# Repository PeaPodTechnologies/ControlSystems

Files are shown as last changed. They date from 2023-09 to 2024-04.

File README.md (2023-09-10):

# PeaPod Microcontroller Software

A library written in Arduino C++ for modular plug-and-play low-level control systems through a high-level API. Implemented with PlatformIO and tested on AVR.

# Overview

The goals of this library are threefold:
1. Error-free asynchronous communication with a **dynamic** list of multiplexers and I2C devices;
2. **Abstraction** from those multiplexer groups into hot-swappable `Module`s, and I2C devices into `Sensor`s (environment variable *getters*) and `Actuator`s (environment variable *setters*);
3. **Mapping** together `Sensor`s and `Actuator`s into coherent `ControlSystem`s: feedback systems, each with a "parameter" that can be set as the target value of the environment variable of interest;

## Installation
> This will eventually be migrated to an Arduino library. For now, see #Development##Installation

# Development

## Testing

`pio test -e peapod`

## API

### Object Instance Tree
```
PeaPod (God Object)
|-ControlSystem*'s HashMap (for instruction handling & calculation)
| |-Control Systems [key: environment variable being controlled]
|   |-Sensor* (envvar getter)
|   |-Actuator* (envvar setter)
|   |-parameter (string)
|   |-target    (float)
|
|-Module List (hardware state change tracking -> Interface lifecycle management)
| |-Sensor* Array
| |-Actuator* Array
| |-Interface* Array (support)
| |-array lengths (byte)
```

### Inheritance Tree

```
Interface
|-ADC
|-EEPROM
|-GPIO
|-PWM
|-Any I2C Sensors/Actuators (multiple inheritance)

Module (MUX device)

Sensor
|-All Sensors

Actuator
|-All Actuators
```

### Dependency Summary

> Not including external libraries or `utils/`.

```
Interface
|-MUX (also included in Interface)
|-All other interfaces
|-All I2C Sensors/Actuators
```

## Style Guide

- Sensor and actuator instance-related code should not be const
- Static API code (i.e. ids, factories) should be const (and preferrably PROGMEM)
- Avoid passing around pointers to const pointers. It's already const.

## Hardware Spec

### Connector Pinouts

- I2C: JST SH 1.00mm 4-pin (1: GND, 2: +5V, 3: SDA, 4: SCL)
- Middleware Output Signals: Molex Micro-Lock PLUS 2-pin (1: Signal, 2: GND)
- Endware Recieving Signals: Molex Micro-Lock PLUS 2-pin (1: GND, 2: Signal)
- Power: Molex Micro-Fit 3.0 2-pin (1: GND, 2: VCC)

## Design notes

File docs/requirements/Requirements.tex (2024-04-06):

\documentclass{../../../../docs/tex/report}
\usepackage{setspace} % Setting line spacing
\usepackage{ulem} % Underline
\usepackage{caption} % Captioning figures
\usepackage{subcaption} % Subfigures
\usepackage{geometry} % Page layout
\usepackage{multicol} % Columned pages
\usepackage{array,etoolbox}
\usepackage{fancyhdr}
\usepackage{enumitem}
\usepackage[toc,page]{appendix}

% Page layout (margins, size, line spacing)
\geometry{letterpaper, left=1in, right=1in, bottom=1in, top=1in}
\setstretch{1.5}

% Headers
\pagestyle{fancy}
\lhead{PeaPod for XYZ - Requirements}
\rhead{PeaPod Technologies Inc.}

% Metric counter, referencing commands
\newcounter{metricnumber}
\setcounter{metricnumber}{1}
\newcommand{\metricrow}{M\arabic{metricnumber}}
\newcommand{\mlabel}[1]{\addtocounter{metricnumber}{-1}\refstepcounter{metricnumber}\label{#1}\addtocounter{metricnumber}{1}}
\newcommand{\mref}[1]{\hyperref[#1]{M\ref{#1}}}

\begin{document}

\begin{titlepage}
    \begin{center}
        \vspace*{1.2cm}

        \textbf{\large{PeaPod for XYZ - Requirements}}

        \vspace{0.5cm}

        Outlining the Implementation-Specific Requirements for a PeaPod XYZ\\

        \textit{Extends: \textbf{PeaPod - Requirements}}

        \vfill
        \input{../../../../docs/tex/documentation/Namecard.tex}
        \vspace{1.25cm}

        Revision 0.1\\
        PeaPod Technologies Inc.\\
        March 31st, 2024

    \end{center}
\end{titlepage}

\thispagestyle{plain}

\tableofcontents
\newpage

\section{Introduction}
\label{sec:intro}

\subsection{Purpose}
\label{sec:purpose}

The purpose of this document is to outline both the category requirements (Section \ref{sec:requirements}) for an implementation of the PeaPod framework (See \textit{PeaPod - Requirements}) that XYZ and the scoped requirements (Section \ref{sec:scope}) for the design being proposed by PeaPod Technologies Inc.: \textbf{PeaPod for XYZ}.

\subsection{Design Paradigm}
\label{sec:structure}

\input{../../../../docs/tex/documentation/DesignParadigm.tex}

\clearpage

\subsection{Scope and Justification}
\label{sec:scope}

\begin{enumerate}[label=SC\arabic*., ref=SC\arabic*]
    \item \label{sc:1} Lorem ipsum dolor sit amet, consectetur adipiscing elit:
    \begin{enumerate}[label=SC3\alph*., ref=SC3\alph*]
        \item \label{sc:1a} Sed auctor, nunc nec ultricies ultricies, nunc nunc ultricies nunc, nec ultricies nunc nunc nec.
    \end{enumerate}
\end{enumerate}

\subsection{Definitions}
\label{sec:definitions}

A number of useful definitions have emerged from the above scoping:
\begin{enumerate}
    \item \textbf{ABC} - Lorem ipsum dolor sit amet, consectetur adipiscing elit.
\end{enumerate}

\clearpage

\section{Framing}
\label{sec:framing}

\subsection{Problem Statement}
\label{sec:opportunity}

Lorem ipsum dolor sit amet, consectetur adipiscing elit. Sed auctor, nunc nec ultricies ultricies, nunc nunc ultricies nunc, nec ultricies nunc nunc nec.

\subsection{Solution Requirements}
\label{sec:requirements}

The following are the overall challenge requirements compiled from A, B, and an excerpt from C:
\begin{enumerate}[label=R\arabic*., ref=R\arabic*]
    \item \label{r:1} \textbf{Must} lorem ipsum dolor sit amet, consectetur adipiscing elit:
    \begin{enumerate}[ref=R1\alph*]
        \item \label{r:1a} \textbf{Should} lorem ipsum dolor sit amet, consectetur adipiscing elit;
    \end{enumerate}
\end{enumerate}

% Change line spacing for the more list-heavy sections
\setstretch{1}
\subsection{Stakeholders and Values}
\label{sec:stakeholders}

\begin{enumerate}[label=S\arabic*., ref=S\arabic*]
    \item \label{s:1} A - Values, etc.
    \item \label{s:2} B - DfX, etc.
\end{enumerate}

\clearpage

\subsection{Problem-Solving Goals}
\label{sec:goals}

% High-Level
\begin{multicols}{2}[]
    \begin{enumerate}[label=HL\arabic*., ref=HL\arabic*]
        \item \label{hl:output} Goal ABC \hfill (\ref{s:1}, \ref{r:1}, \ref{r:1a})
    \end{enumerate}
\end{multicols}

\subsection{Solution Objectives}
\label{sec:objectives}

% Low-Level
\begin{multicols}{2}[]
    \begin{enumerate}[label=LL\arabic*., ref=LL\arabic*]
        \item \label{ll:output_variety} Objective ABC \hfill (\ref{hl:output})
    \end{enumerate}
\end{multicols}

\clearpage

\subsection{Metrics}
\label{sec:metrics}

\begin{tabular}{| @{\makebox[2.4em][c]{\metricrow}} | p{8.7cm} | p{5.9cm} |} 
    \hline
    \multicolumn{1}{| @{\makebox[2.4em][c]{\textbf{\#}}} | l |}{\textbf{Metric}} & \textbf{Units}\\ 
    \hline
    Metric ABC \mlabel{m:constraint} \hfill (\ref{ll:output_variety}) & Yes/No \\
    Metric XYZ \mlabel{m:criteria} \hfill (\ref{ll:output_variety}) & 0 - 100\% \\
    \hline
\end{tabular}

\clearpage

\subsection{Constraints}
\label{sec:constraints}

\begin{tabular}{|l|p{14.35cm}|}
    \hline
    \textbf{Metric} & \textbf{Constraint \hfill Justification} \\
    \hline
    \mref{m:constraint} & Yes \hfill (\ref{s:1})\\
    \hline
\end{tabular}

\subsection{Criteria}
\label{sec:criteria}

\begin{tabular}{|l|p{14.35cm}|}
    \hline
    \textbf{Metric} & \textbf{Criteria \hfill Justification} \\
    \hline
    \mref{m:criteria} & Should Maximize \hfill (\ref{r:1a}) \\
    \hline
\end{tabular}

% Refer to Appendix \ref{sec:assessment} for prototype verification Assessment Criteria (categories, weights, etc.).

\newpage

\section{Reference Designs}

% -------- TEMPLATE --------
% Introduction - Project goal, scope, differences from this project
% Graphics - Design drawings/photos, etc.
% Analysis - Rank the design across each of our metrics
    % TODO: Metrics might be too much, maybe just qualitative analysis based on LLOs?

\subsection{Reference Design XYZ}

Lorem ipsum dolor sit amet, consectetur adipiscing elit. Sed auctor, nunc nec ultricies ultricies, nunc nunc ultricies nunc, nec ultricies nunc nunc nec.

% \newpage

% % References
% \bibliographystyle{IEEEtran}
% \bibliography{references}

\end{document}

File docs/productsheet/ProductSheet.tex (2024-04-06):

\documentclass{../../../../docs/tex/report}
\usepackage{setspace} % Setting line spacing
\usepackage{ulem} % Underline
\usepackage{caption} % Captioning figures
\usepackage{subcaption} % Subfigures
\usepackage{geometry} % Page layout
\usepackage{multicol} % Columned pages
\usepackage{array,etoolbox}
\usepackage{fancyhdr}
\usepackage{enumitem}
\usepackage[toc,page]{appendix}
\setlist{noitemsep}

% Page layout (margins, size, line spacing)
\geometry{letterpaper, left=1in, right=1in, bottom=1in, top=1in}
\setstretch{1}

% Headers
\pagestyle{fancy}
\lhead{PeaPod XYZ}
\rhead{PeaPod Technologies Inc.}

\begin{document}

\begin{titlepage}
    \begin{center}
        \vspace*{1.2cm}

        \textbf{\large{PeaPod XYZ - Product Sheet}}

        \vspace{0.5cm}

        Lorem ipsum dolor sit amet, consectetur adipiscing elit.

        \vfill
        \input{../../../docs/tex/documentation/Namecard.tex}
        \vspace{1.25cm}

        Revision 0.1\\
        PeaPod Technologies Inc.\\
        Month XX, 2024

    \end{center}
\end{titlepage}

\thispagestyle{plain}

\tableofcontents
\clearpage

\section{Product Overview}

\subsection{Introduction}

Lorem ipsum dolor sit amet, consectetur adipiscing elit. Sed auctor, nunc nec ultricies ultricies, nunc nunc ultricies nunc, nec ultricies nunc nunc nec. Sed auctor, nunc nec ultricies ultricies, nunc nunc ultricies nunc, nec ultricies nunc nunc nec. Sed auctor, nunc nec ultricies ultricies, nunc nunc ultricies nunc, nec ultricies nunc nunc nec. Sed auctor, nunc nec ultricies ultricies, nunc nunc ultricies nunc, nec ultricies nunc nunc nec.

\clearpage

% References
\bibliographystyle{IEEEtran}
\bibliography{references}
\end{document}

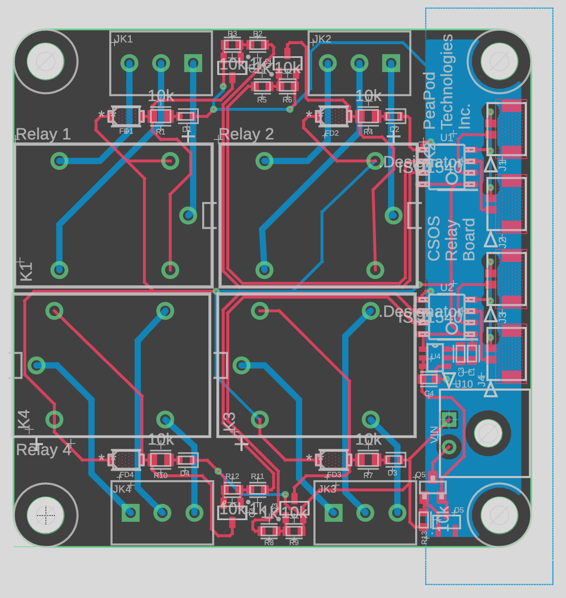
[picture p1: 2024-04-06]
hardware/relay/schematics/relay_brd.png

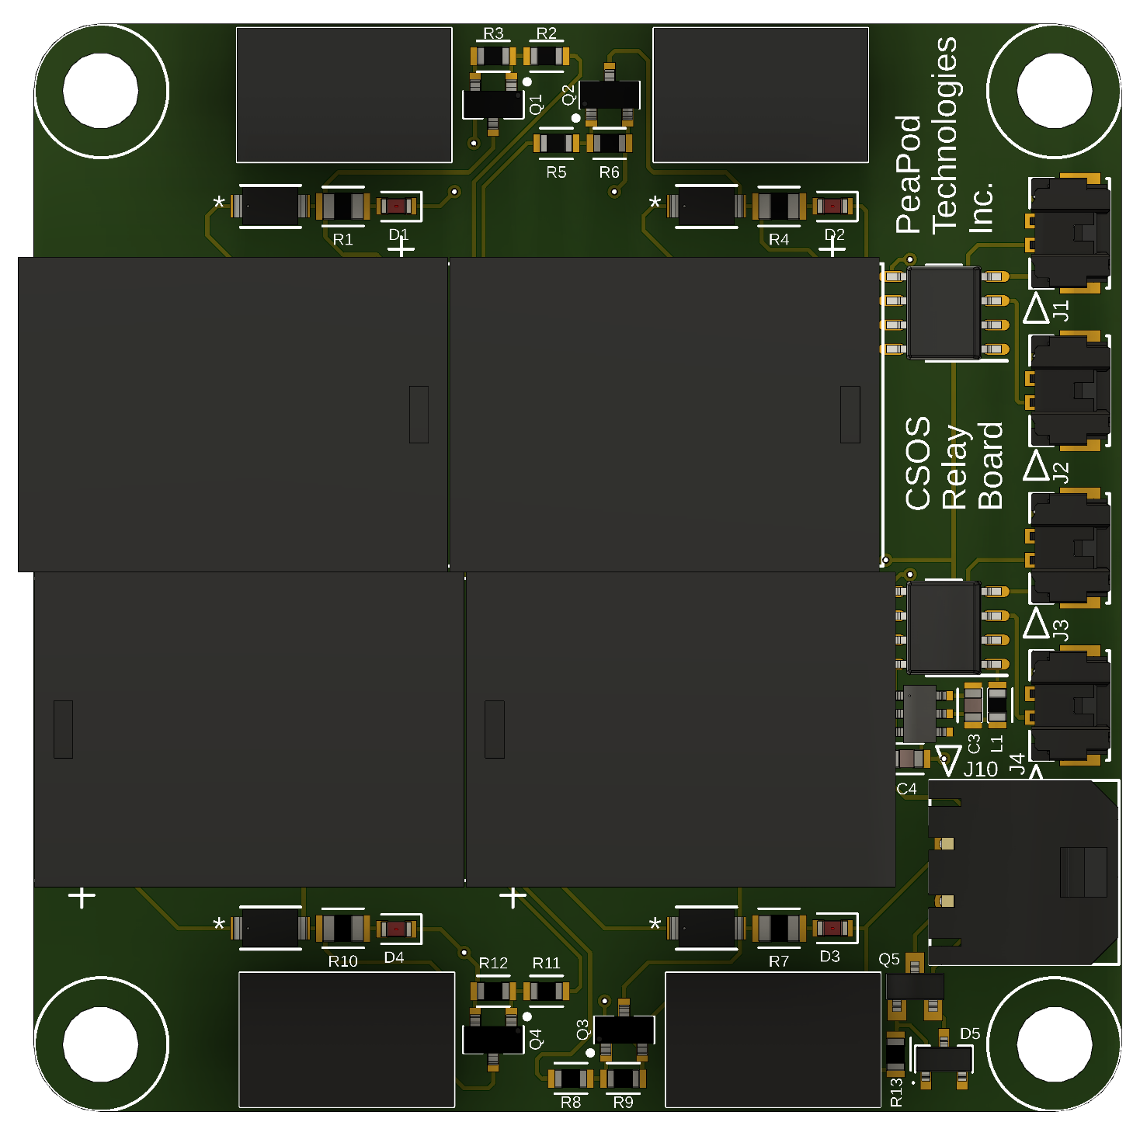
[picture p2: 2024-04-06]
hardware/relay/relay_model.png

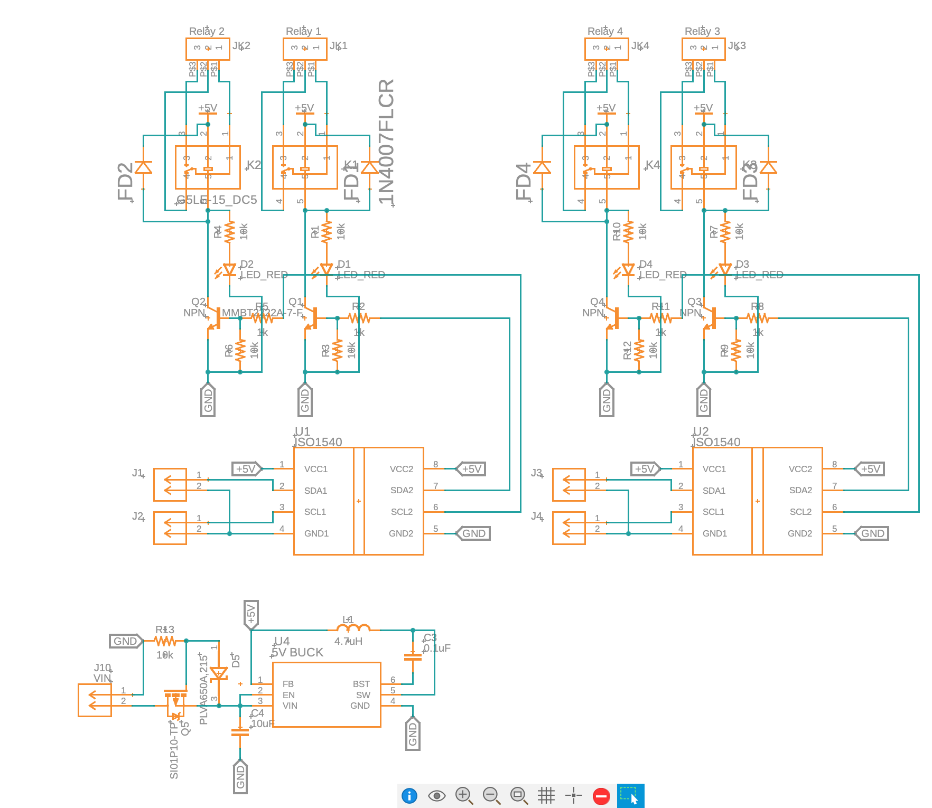
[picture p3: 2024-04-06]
hardware/relay/schematics/relay_sch.png

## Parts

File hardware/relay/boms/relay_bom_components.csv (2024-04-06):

Index | Manufacturer Part Number | Manufacturer Name | Requested Quantity 1 | Pack Quantity 1 | Pack Type 1 | Digi-Key Part Number 1 | Unit Price 1 | Extended Price 1 | Minimum Order Quantity 1 | Reference Designator | Product Notes
1 | PLVA650A,215 | Nexperia USA Inc. | 1 | 1 | Cut Tape (CT) | 1727-5167-1-ND | 0.65000 | $0.65 | 1 | D5
2 | SI01P10-TP | Micro Commercial Co | 1 | 1 | Cut Tape (CT) | 353-SI01P10-TPCT-ND | 0.59000 | $0.59 | 1 | Q5
3 | AP63205WU-7 | Diodes Incorporated | 1 | 1 | Cut Tape (CT) | AP63205WU-7DICT-ND | 1.33000 | $1.33 | 1 | U4
4 | 0436500201 | Molex | 1 | 1 | Tray | WM1865-ND | 2.00000 | $2.00 | 1 | J10
5 | G5LE-14 DC5 | Omron Electronics Inc-EMC Div | 4 | 4 | Tray | Z1011-ND | 2.38000 | $9.52 | 1 | K1,K2,K3,K4
6 | 1N4007FL | SMC Diode Solutions | 4 | 4 | Cut Tape (CT) | 1655-1N4007FLCT-ND | 0.19000 | $0.76 | 1 | FD1,FD2,FD3,FD4
7 | ISO1540D | Texas Instruments | 2 | 2 | Tube | 296-34896-5-ND | 9.46000 | $18.92 | 1 | U1,U2
8 | 5055670271 | Molex | 4 | 4 | Cut Tape (CT) | WM17038CT-ND | 1.32000 | $5.28 | 1 | J1,J2,J3,J4
9 | 0393570003 | Molex | 4 | 4 | Bag | WM7878-ND | 2.67000 | $10.68 | 1 | JK1,JK2,JK3,JK4
10 | CL10B104KB8NNWC | Samsung Electro-Mechanics | 1 | 1 | Cut Tape (CT) | 1276-1935-1-ND | 0.14000 | $0.14 | 1 | C3
11 | LQM18PH4R7MFRL | Murata Electronics | 1 | 1 | Cut Tape (CT) | 490-LQM18PH4R7MFRLCT-ND | 0.57000 | $0.57 | 1 | L1
12 | CL10A106MQ8NNNC | Samsung Electro-Mechanics | 1 | 1 | Cut Tape (CT) | 1276-1119-1-ND | 0.16000 | $0.16 | 1 | C4
13 | MMBT2222A-7-F | Diodes Incorporated | 4 | 4 | Cut Tape (CT) | MMBT2222A-FDICT-ND | 0.21000 | $0.84 | 1 | Q1,Q2,Q3,Q4
14 | LTST-C191KRKT | Lite-On Inc. | 4 | 4 | Cut Tape (CT) | 160-1447-1-ND | 0.40000 | $1.60 | 1 | D1,D2,D3,D4
15 | RC0603FR-0710KL | YAGEO | 5 | 5 | Cut Tape (CT) | 311-10.0KHRCT-ND | 0.15000 | $0.75 | 1 | R3,R6,R9,R12,R13
16 | RC0805FR-0710KL | YAGEO | 4 | 4 | Cut Tape (CT) | 311-10.0KCRCT-ND | 0.15000 | $0.60 | 1 | R1,R4,R7,R10
17 | RC0603FR-071KL | YAGEO | 4 | 4 | Cut Tape (CT) | 311-1.00KHRCT-ND | 0.15000 | $0.60 | 1 | R2,R5,R8,R11

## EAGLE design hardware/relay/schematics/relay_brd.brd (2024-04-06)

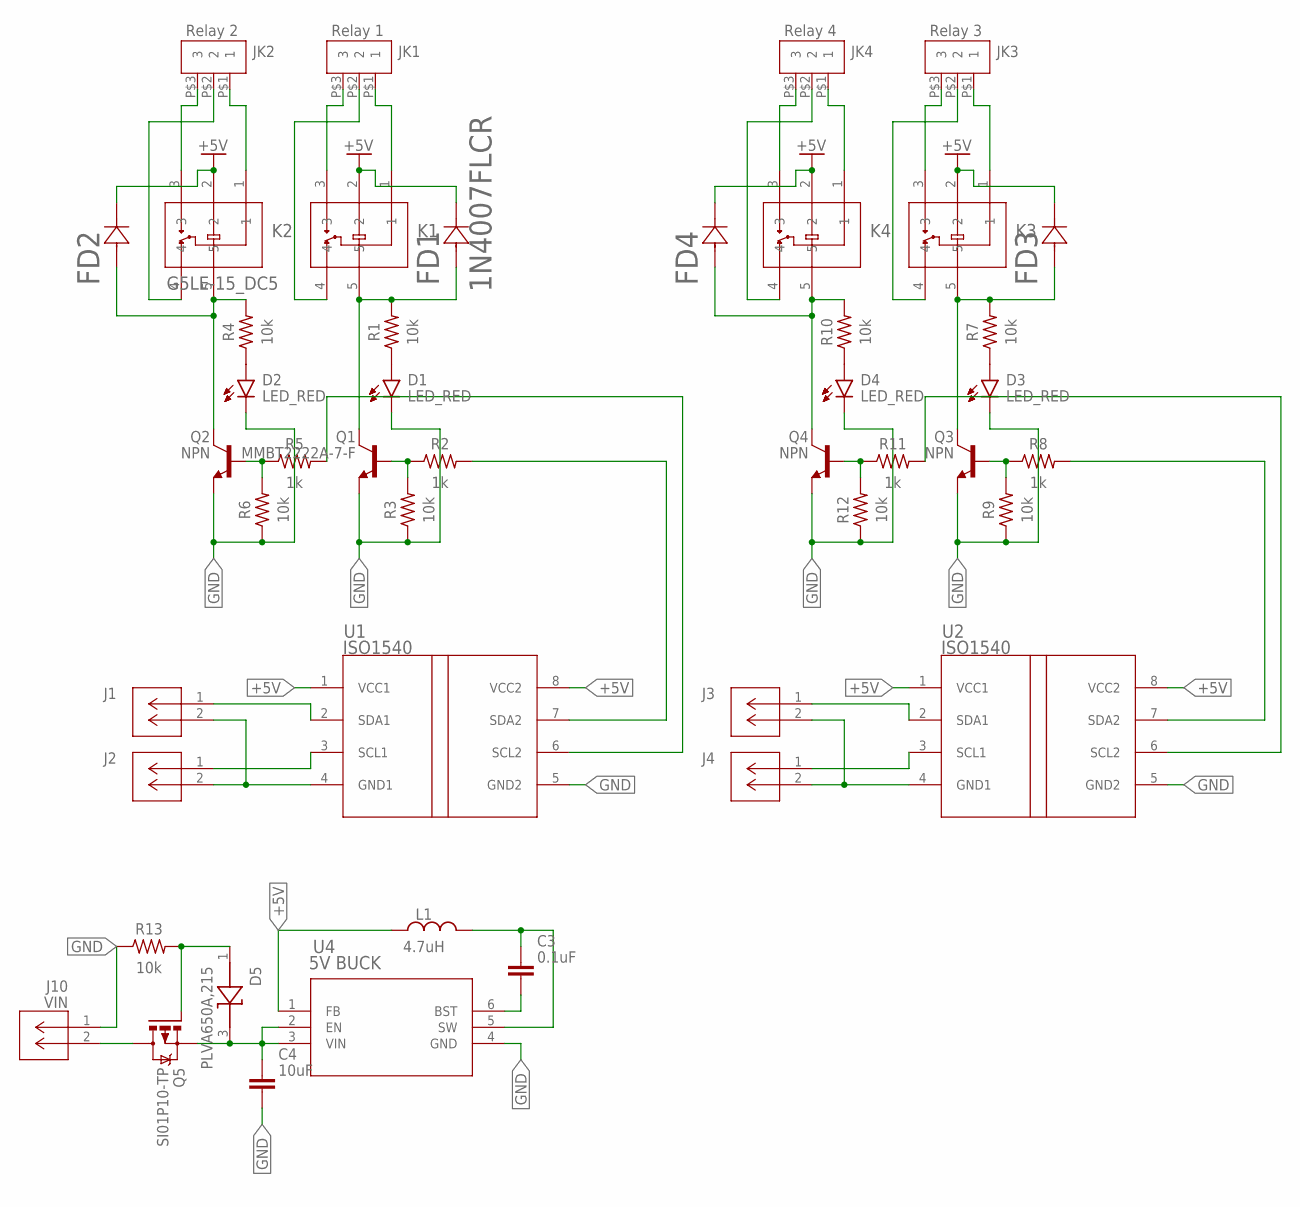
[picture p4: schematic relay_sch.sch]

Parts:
C3: 0.1uF; CAPC1608X85
C4: 10uF; CAPC1608X85
D1, D2, D3, D4: LED_RED; LEDC1608X55N_FLAT-R
D5: PLVA650A,215; SOT95P230X110-3N
FD1: 1N4007FLCR; CR_SOD-123FL_SME-L
FD2, FD3, FD4: 1N4007FLCR_SOD-123FL_SME-L; CR_SOD-123FL_SME-L
J1, J2, J3, J4: MICROLOCK-2PIN; 2PIN
J10: VIN; 2PIN
JK1: Relay 1; TERM-3,5MM
JK2: Relay 2; TERM-3,5MM
JK3: Relay 3; TERM-3,5MM
JK4: Relay 4; TERM-3,5MM
K1, K3, K4: G5LE-14_DC12RELAY_G5LE-1_DC5_OMR; RELAY_G5LE-1_DC5_OMR
K2: G5LE-15_DC5; RELAY_G5LE-1_DC5_OMR
L1: 4.7uH; INDC1608X95N
Q1: MMBT2222A-7-F; SOT95P237X112-3N
Q2, Q3, Q4: NPN; SOT95P237X112-3N
Q5: SI01P10-TP; SOT23
R1, R4, R7, R10: 10k; RESC2012X65
R2, R5, R8, R11: 1k; RESC1608X60
R3, R6, R9, R12, R13: 10k; RESC1608X60
U1, U2: ISO1540; SOIC-8
U4: 5V BUCK; AP63205

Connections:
+5V: FD1.1 (CATHODE), FD2.1 (CATHODE), FD3.1 (CATHODE), FD4.1 (CATHODE), K1.2, K2.2, K3.2, K4.2, L1.1, U1.1 (VCC1), U1.8 (VCC2), U2.1 (VCC1), U2.8 (VCC2), U4.1 (FB)
GND: C4.2, D1.C, D2.C, D3.C, D4.C, J10.1, Q1.2 (E), Q2.2 (E), Q3.2 (E), Q4.2 (E), R3.1, R6.1, R9.1, R12.1, R13.1, U1.5 (GND2), U2.5 (GND2), U4.4 (GND)
unnamed: JK1.P$3 (3), K1.3
unnamed: JK1.P$1 (1), K1.1
unnamed: JK1.P$2 (2), K1.4
unnamed: FD1.2 (ANODE), K1.5, Q1.3 (C), R1.2
unnamed: FD2.2 (ANODE), K2.5, Q2.3 (C), R4.2
unnamed: Q1.1 (B), R2.1, R3.2
unnamed: JK2.P$3 (3), K2.3
unnamed: R2.2, U1.7 (SDA2)
unnamed: J1.1 (2), U1.2 (SDA1)
unnamed: J2.1 (2), U1.3 (SCL1)
unnamed: J1.2 (3), J2.2 (3), U1.4 (GND1)
unnamed: JK2.P$1 (1), K2.1
unnamed: FD4.2 (ANODE), K4.5, Q4.3 (C), R10.2
unnamed: FD3.2 (ANODE), K3.5, Q3.3 (C), R7.2
unnamed: Q2.1 (B), R5.1, R6.2
unnamed: JK2.P$2 (2), K2.4
unnamed: R5.2, U1.6 (SCL2)
unnamed: JK3.P$3 (3), K3.3
unnamed: JK3.P$1 (1), K3.1
unnamed: D2.A, R4.1
unnamed: D3.A, R7.1
unnamed: Q3.1 (B), R8.1, R9.2
unnamed: JK3.P$2 (2), K3.4
unnamed: J3.1 (2), U2.2 (SDA1)
unnamed: R8.2, U2.7 (SDA2)
unnamed: J4.1 (2), U2.3 (SCL1)
unnamed: J3.2 (3), J4.2 (3), U2.4 (GND1)
unnamed: JK4.P$3 (3), K4.3
unnamed: JK4.P$1 (1), K4.1
unnamed: D1.A, R1.1
unnamed: D4.A, R10.1
unnamed: Q4.1 (B), R11.1, R12.2
unnamed: JK4.P$2 (2), K4.4
unnamed: R11.2, U2.6 (SCL2)
unnamed: C3.2, U4.6 (BST)
unnamed: C3.1, L1.2, U4.5 (SW)
unnamed: J10.2, Q5.3 (D)
unnamed: C4.1, D5.3 (C), Q5.2 (S), U4.2 (EN), U4.3 (VIN)
unnamed: D5.1 (A), Q5.1 (G), R13.2

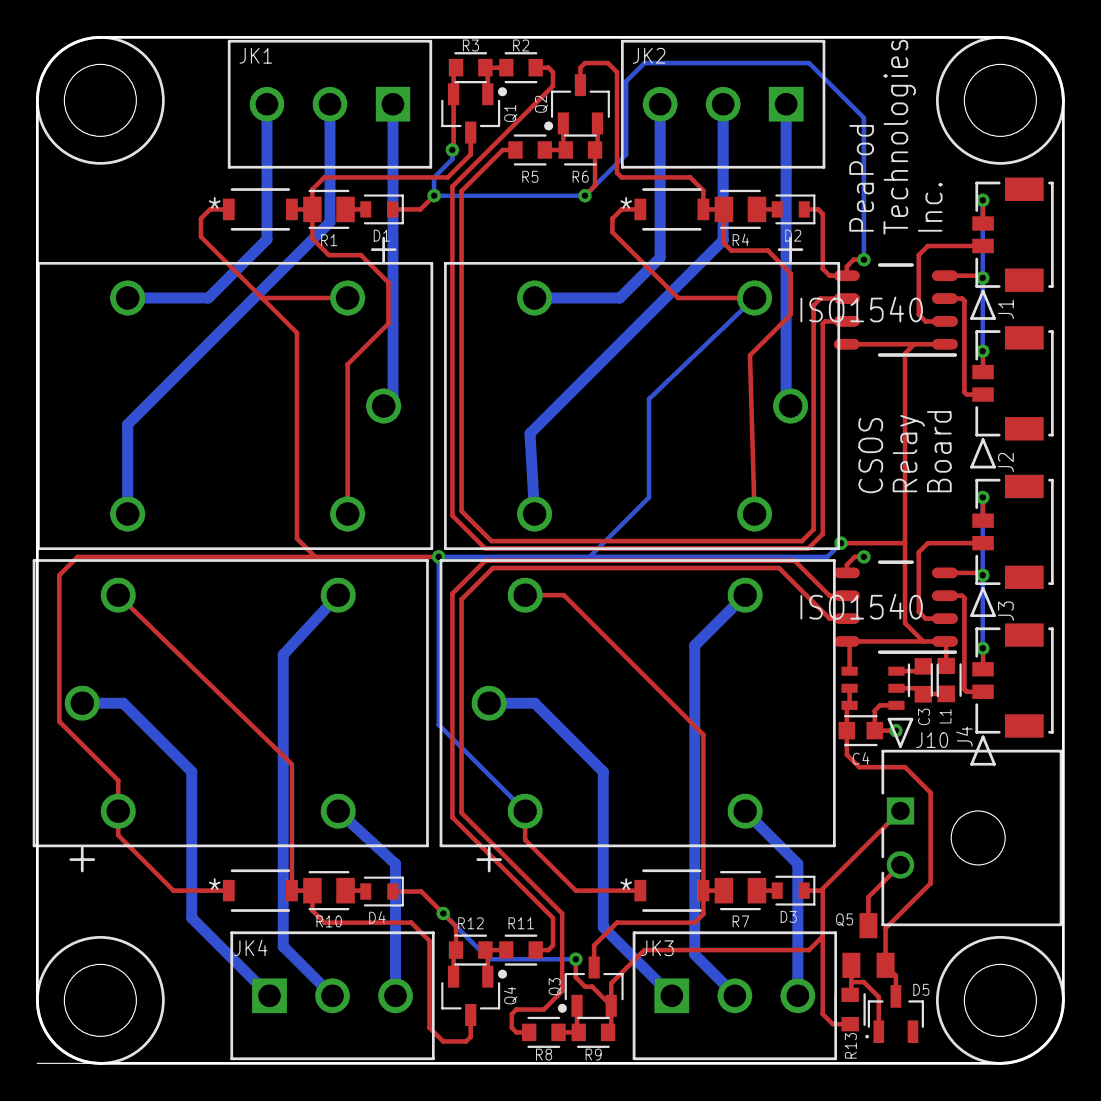
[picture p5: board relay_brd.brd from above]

Board: 2 copper layers, 57.0 x 57.0 mm, 46 parts (0 on the bottom side), 41 nets.

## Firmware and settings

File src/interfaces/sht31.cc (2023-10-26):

#include <interfaces/sht31.h>

static uint8_t crc8(const uint8_t *data, int len) {
  /*
   *
   * CRC-8 formula from page 14 of SHT spec pdf
   *
   * Test data 0xBE, 0xEF should yield 0x92
   *
   * Initialization data 0xFF
   * Polynomial 0x31 (x8 + x5 +x4 +1)
   * Final XOR 0x00
   */

  const uint8_t POLYNOMIAL(0x31);
  uint8_t crc(0xFF);

  for (int j = len; j; --j) {
    crc ^= *data++;

    for (int i = 8; i; --i) {
      crc = (crc & 0x80) ? (crc << 1) ^ POLYNOMIAL : (crc << 1);
    }
  }
  return crc;
}

using namespace ControlSystemsOS;

SHT31::SHT31(const i2cip_fqa_t& fqa, const i2cip_id_t& id) : Device(fqa, id), InputInterface<state_sht31_t, args_sht31_t>((Device*)this) { }

i2cip_errorlevel_t SHT31::get(state_sht31_t& value, const args_sht31_t& args) {
  size_t buflen = 6;
  uint8_t buffer[buflen];

  #ifdef CSOS_DEBUG_SERIAL
    DEBUG_DELAY();
    CSOS_DEBUG_SERIAL.print(F("!!! SHT31 GET !!!"));
    DEBUG_DELAY();
  #endif

  // Read registers
  i2cip_errorlevel_t errlev = this->readRegister(SHT31_MEAS_HIGHREP_STRETCH, buffer, buflen, false);
  I2CIP_ERR_BREAK(errlev);

  if (buflen != sizeof(buffer)) {
    return I2CIP_ERR_SOFT; 
  }

  // Checksum
  if (buffer[2] != crc8(buffer, 2) || buffer[5] != crc8(buffer + 3, 2)) {
    return I2CIP_ERR_SOFT;
  }

  // Temperature conversion
  int32_t stemp = (int32_t)(((uint32_t)buffer[0] << 8) | buffer[1]);
  stemp = ((4375 * stemp) >> 14) - 4500;
  value.temperature = (float)stemp / 100.0f;

  // Humidity conversion
  uint32_t shum = ((uint32_t)buffer[3] << 8) | buffer[4];
  shum = (625 * shum) >> 12;
  value.humidity = (float)shum / 100.0f;

  #ifdef CSOS_DEBUG_SERIAL
    DEBUG_DELAY();
    CSOS_DEBUG_SERIAL.print(F("!!! "));
    CSOS_DEBUG_SERIAL.print(value.temperature);
    CSOS_DEBUG_SERIAL.print(F("C, "));
    CSOS_DEBUG_SERIAL.print(value.humidity);
    CSOS_DEBUG_SERIAL.print(F("% !!!"));
    DEBUG_DELAY();
  #endif

  return I2CIP_ERR_NONE;
}

const args_sht31_t& SHT31::getDefaultA(void) const {
  return this->default_a;
}

void SHT31::clearCache(void) {
  this->setCache(this->default_cache);
}

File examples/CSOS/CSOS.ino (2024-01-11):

#define MAIN true

#include <Arduino.h>

#include <debug.h>

#include <ControlSystemsOS.h>
#include <chrono.h>

#define FIXED_UPDATE_DELTA 1000

fsm_timestamp_t start = 0;
fsm_timestamp_t lastFixedUpdate = 0;

bool rebuild = false;

void setup(void) {
  // Serial
  Serial.begin(115200);
  while(!Serial);

  start = millis();

  Serial.println("==== [ CYCLE 0 (BUILD) ] ====");

  delay(1000);

  i2cip_errorlevel_t errlev = ControlSystemsOS::update(true);
  if(errlev > I2CIP_ERR_NONE) {
    Serial.println("==== [ BUILD FAILED, FREEZING ] ====");
    while(true) { // Blink
      digitalWrite(LED_BUILTIN, HIGH);
      delay(100);
      digitalWrite(LED_BUILTIN, LOW);
      delay(100);
    }
  }
}

uint8_t cycle = 0;

void loop(void) {
  cycle++;
  Serial.print("\n\n==== [ CYCLE ");
  Serial.print(cycle);
  Serial.println(" ] ====");

  delay(1000);

  fsm_timestamp_t cyclestart = millis();
  
  // 1. Refresh Update - Network Status Handling & Rebuild

  // 1a. Module "Roll-Call" Check
  i2cip_errorlevel_t errlev = ControlSystemsOS::update(rebuild);
  // If we lose hardware, return and do rebuild ASAP
  rebuild = (errlev == I2CIP_ERR_HARD);
  if(errlev > I2CIP_ERR_NONE) return;

  // 1b. Module Control Systems Refresh
  fsm_timestamp_t now = millis();
  if((now - lastFixedUpdate) > FIXED_UPDATE_DELTA) {
    errlev = ControlSystemsOS::fixedUpdate(now);
    lastFixedUpdate = millis();
  }
}

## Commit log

2022-11-10 CSOS v0.1.1 - GPIO, PWM, ADC Libraries
2023-10-25 INTEGRATED I2CIP
2024-04-06 Relay Board and Docs V1
    [relay_bom_components.csv, relay_brd.brd, relay_sch.sch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]

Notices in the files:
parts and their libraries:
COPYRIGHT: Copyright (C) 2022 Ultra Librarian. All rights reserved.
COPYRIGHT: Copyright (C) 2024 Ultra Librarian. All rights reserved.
